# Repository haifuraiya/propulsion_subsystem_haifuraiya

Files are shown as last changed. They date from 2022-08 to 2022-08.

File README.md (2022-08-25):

# propulsion_subsystem_haifuraiya
# Introduction

This Open Research Institute Phase4SPace project repo will be used to develop the proposed Haifuraiya (Japanese:  ハイフライヤー English: High-Flyer) propulsion subsystem for a future HEO mission SmallSat. The repo was created on 8/28/2022.

# Summary

In July/August 2022 the ORI community discussed formalizing a concept for a High Energy Orbit (HEO) 'flyer' satellite, that would have its own propulsion system. The background for the Haifuraiya name and the overall initial concept derivation/top-level goals was discussed at length and is recorded[^1] and its predecessor concept by Jan King W3GEY is directly available[^2]. 

# Team

1. Samudra Haque N3RDX
2. Dan Schultz N8FGV
3. Thomas Denz, KC3ELI

# Special Notes

By special arrangement with its inventor/develpoer, ORI is making available in this repository a public copy of the entire flight hardware designs/firmware build knowledge-base including a comprehensive technical, scientific and industrial documentation set of [The George Washington University][100] [Micro-propulsion and Nanotechnology Laboratory][99]'s successful 2014-2015 BRICSAT-P (US Naval Academy/George Washington University) and 2014-2018 Canyval-X (Yonsei University/NASA GSFC/George Washington University) CubeSat quad-channel electric rocket system as provided in 2015 to NASA, on the condition that it is only used for study/research/experimentation/academic and scientific missions, and no commercial development is allowed. Parts of the technology have been patented (US Patent 10006445) and is available for licensing from The George Washington University. 

The knowledge-base is available [here][101]

If you choose to view/utilize the references (Approximately *3.14GB, 3525 files*), you are advised the knowledge-base contains copyrighted code, and information that was and still could be of a propietary nature thus may have more restrictive licenses than the license under which ORI has organized this repository. Your are restricted from disseminating this repository without the exact same restrictions you are being asked to follow. *While ORI has assurances the information will be able to be replicated (to build ground/engineering/flight hardware) with current production COTS parts -  there is no technical support provided, and all questions are to be redirected to the inventor/developer directly. Contact ORI for further details.* 

# References

[^1]: [Haifuraiya slide presentations (August 2022)][1]
[^2]: [HEO-F Mission Overview Space System Design Concept (November 3, 2014)]

[1:] https://github.com/phase4ground/documents/tree/master/Papers_Articles_Presentations/Slide_Presentations/haifuraiya/   
[2:] https://github.com/phase4ground/documents/blob/master/Papers_Articles_Presentations/Slide_Presentations/haifuraiya/HEO-F_Mission%20Overview.pptx  
[99:]https://mpnl.seas.gwu.edu/
[100:] https://www.gwu.edu
[101:] TBD

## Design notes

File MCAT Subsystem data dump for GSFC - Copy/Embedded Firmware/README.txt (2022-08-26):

3/24/2015 Samudra Haque samudra@gwu.edu GWU MAE MpNL
This codebase requires Netburner NANO54415 network development kit (NNDK).
It depends upon the Netburner RTOS and libraries obtained through the typical free developer license, which depends upon the use of an unmodified netburner module, hence the use of a daughter board approach for the Control Unit in a Mini-PCI Express connector/latch.

www.netburner.com

The codebase is 6C. Developed for the BRICSAT-P platform originally (Oct, 2015). Any .s19 extension file is a hex binary to be downloaded to a netburner NANO54415 target. GROUNDTESTING and FLIGHT modes enable/disable verbosity.

Choose the configuration you need to compile for, from the NBECLIPSE project properties page. 

Future versions:
(from e-mail to CANYVAL-X GSFC/GWU team of 3/16/2015) 

3. For the next few steps, leading to the Month of April, with Azimi's help from GSFC I propose to send Yonsei team (or Phil@Yonsei) my planned software mods are as follows:

2A. 3/15/2015 - COMPLETED - Initial load of MCAT canyval will be the 6C flight code of BRICSAT. No Changes. Command Set 6C. No I2C. Serial Comms only.

2B.3/16/2015 - Version 6D - Modification of low-level timing trigger pulse duration to accomodate Canyval IES (Inductive Energy Storage) specs instead of Bricsat IES specs. This will increase slightly increase the on-time of the IGBT in clamped inductive storage operation, No other changes. No I2C. Serial Comms only. Adjustment of command set for firing rates in five segments A...F to represent likely conops. Currently, this is 1/10/20/30/40/50 Hz. Is this sufficient ?

4. The following steps will be done when practical .... between GWU/GSFC collaboration. (Requires use of a backup MCAT Canyval subsystem or the MCAT Bricsat subsystem, and Azimi Benham's GOMSPACE I2C).

2C.  Version 6E - Addition of I2C comms with interface between Serial Command Buffer / I2C RX, and Telemetry Buffer / I2C TX modules. Commands will be programmed and tested from a GOMSPACE (or any other compatible multi-master I2C device at 400 kHz baud rate) to demo  I2C functions. No changes to command set 6C, unless minor and requested by CANYVAL flight team and approved by Phil.

2D. Version 6F - Addition of current sensor functionality, storage of sensor events, transfer of sensor events to I2C telemetry buffer, testing of Polling feature of sensor events via Telemetry buffer on the I2C bus.

Brief Explanation of the low-level timing routines:
This system uses a hardware DMA timer (could be any hardware timer) that is programmable and executes an interrupt-service routine that inspects the value of the time slice counter. Depending upon the hardware timer values, and the programmed counts, different low-level events can be actuated via the GPIO pins of the Control Unit. This behavior is intended to be implemented as several timing sources, allowing variable pulse repetition rate of different thruster channels, and event triggers, but in this implementation is limited to a single source of timing. That said, for a more complex treatment of the options available, refer to US Patent Appl. 14/462,127 and See Note 4 of Schematic MCAT-CANYVAL-BPL-5X1.pdf document.

Actual timing figures are generated using MATLAB DMATIMERV4 script, so ask the technical contact at GWU for proper use.

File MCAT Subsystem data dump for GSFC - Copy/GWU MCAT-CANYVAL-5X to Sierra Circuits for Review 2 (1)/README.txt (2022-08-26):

There are 13 gerber files per PCB set.

The ASSY files are the correct bill of materials

For schematics/board layouts suggestion, see the Eagle directory in the top of the folder tree.

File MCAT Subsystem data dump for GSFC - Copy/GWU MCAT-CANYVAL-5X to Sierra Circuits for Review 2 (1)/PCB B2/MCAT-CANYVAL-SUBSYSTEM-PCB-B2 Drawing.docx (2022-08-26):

Layer Files (V7A prefix)
L1/TopSignal/Component | CMP
L2/TopGround | LY2
L3/Power Plane 1 | L3
L14/Power Plane 2 | L14
L15/BottomGround | L15
L16/BottomSignal/Solder | SOL
Silk Screen CMP | PLC
Silk Screen SOL | PLS
Solder Stop Mask CMP | STC
Solder Stop Mask SOL | STS
Cream Frame CMP | CRC
Cream Frame SOL | CRS
Excellen Drill Data | DDD

X-ray image of PCB displayed on next page.

PCB DRAWING

Subsystem: MCAT | ASSY: MCAT-CANYVAL | P/N: T2 | REV: 5X | 201502241100

By Samudra Haque (samudra@gwu.edu) and George Teel (gteel@gwu.edu), George Washington University, 2/23/2015

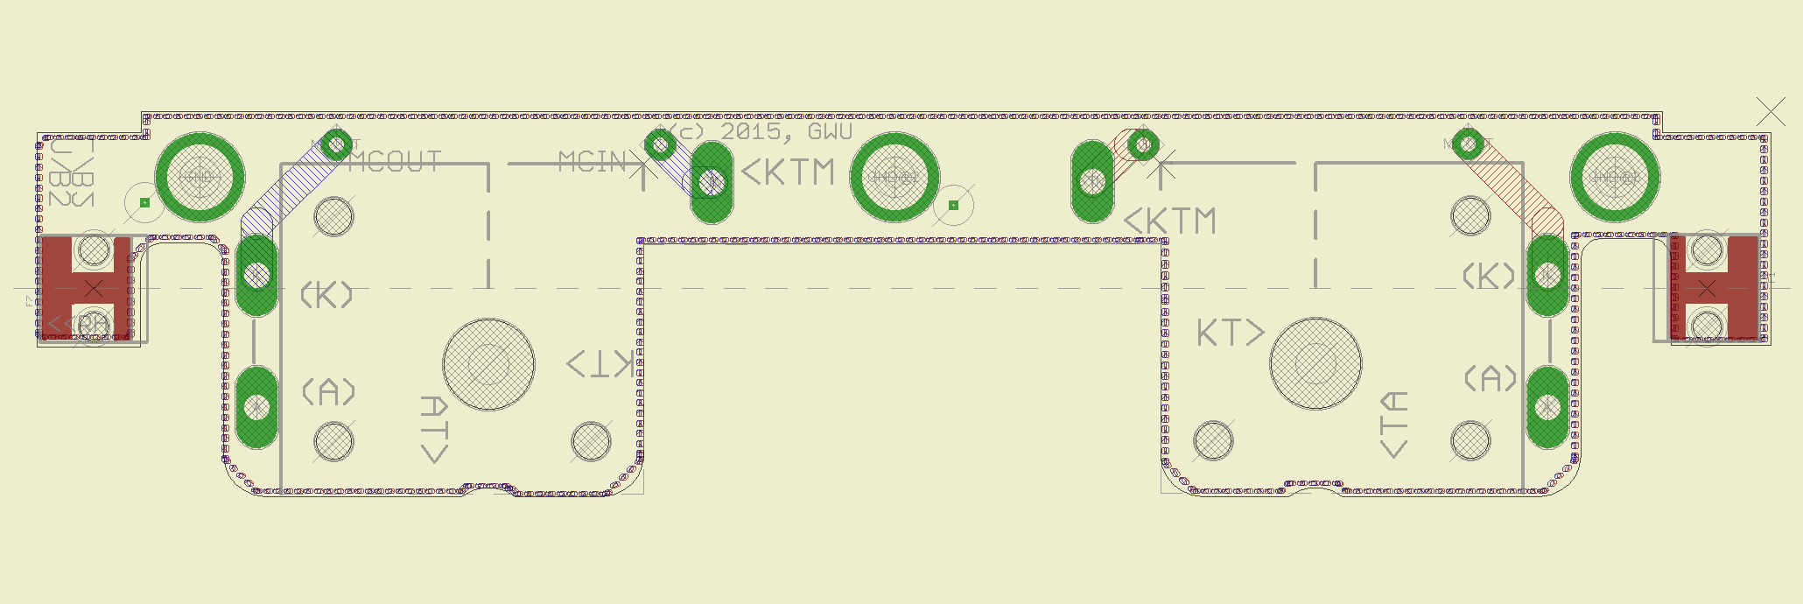
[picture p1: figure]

Notes (unless otherwise specified)

1. Fab per IPC-600G Class 2
2. Material
  a. Lead Free Assembly Compliant, NELCO 7000-3 Toughened POLYIMIDE Laminate & PrEPREG or equiv.
  b. Finished Thickness to be 0.062” +/- .005”
  c. Total of 6 layers with 2 oz. CU ON ALL LAYERS.
  d. FLAMMABILITY RATING: 94 V-O Min.
3. Size: Cut and mill to outline shown; . Datum is BoTTOM/TOP RIGHT CORNER or RIGHT EDGE w/SHARP corner
4. DRILLING: DRILL HOLES PER SCHED. PLATE THROUGH HOLES WITH COPPER, 0.001” THICK MIN.
5. MILLING: PCB OUTLINE PROVIDED
6. ALL HOLE SIZES SPEC. AFTER PLATING.
7. HOLE LOCATION ToL. ARE +/- .003” IN REL. To CTR.
8. FINISH:
  a. HASL
  b. SOLDER MASK OVER BARE COPPER (SMOBC) USING Liquid PHOTO IMAGEABLE (LPI)
  c. COLOR: BOTH SIDES, COLOR BLUE,
  d. SILKSCREEN: WHITE.

Layer functions

L1/Top Signal/Top – 2 Oz Cu.

L2/Top Ground – 2 Oz Cu.

L3/Power Plane 1 – 2 Oz Cu.

L14/Power Plane 2 – 2 Oz Cu.

L15/Bottom Ground – 2 Oz Cu.

L16/Bottom Signal/Bottom – 2 Oz Cu.

MCAT-CANYVAL-B2-5X. 83.82 mm L x 18.64 mm W.

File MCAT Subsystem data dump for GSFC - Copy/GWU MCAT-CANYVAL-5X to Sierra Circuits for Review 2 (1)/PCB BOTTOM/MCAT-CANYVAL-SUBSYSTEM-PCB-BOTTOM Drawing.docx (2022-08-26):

Layer Files
L1/TopSignal/Component | CMP
L2/TopGround | LY2
L3/Power Plane 1 | L3
L14/Power Plane 2 | L14
L15/BottomGround | L15
L16/BottomSignal/Solder | SOL
Silk Screen CMP | PLC
Silk Screen SOL | PLS
Solder Stop Mask CMP | STC
Solder Stop Mask SOL | STS
Cream Frame CMP | CRC
Cream Frame SOL | CRS
Excellen Drill Data | DDD

X-ray image of PCB displayed on next page.

PCB DRAWING

Subsystem: MCAT | ASSY: MCAT-CANYVAL | P/N: BOTTOM | REV: 5X | 201502241100

By Samudra Haque (samudra@gwu.edu) and George Teel (gteel@gwu.edu), George Washington University, 2/23/2015

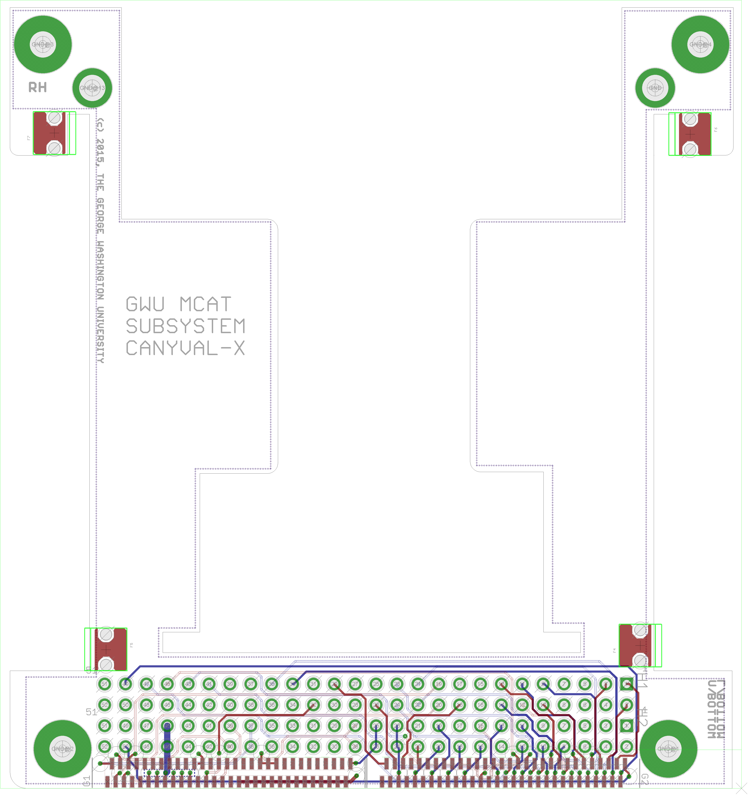
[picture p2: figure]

Notes (unless otherwise specified)

1. Fab per IPC-600G Class 2
2. Material
  a. Lead Free Assembly Compliant, ARLON 85NT or equiv.
  b. Finished Thickness to be 0.062” +/- .005”
  c. Total of 6 layers with 2 oz. CU ON ALL LAYERS.
3. Size: Cut and mill to outline shown; . Datum is BoTTOM RIGHT CORNER
4. DRILLING: DRILL HOLES PER SCHED. PLATE THROUGH HOLES WITH COPPER, 0.001” THICK MIN.
5. MILLING: PCB OUTLINE PROVIDED
6. ALL HOLE SIZES SPEC. AFTER PLATING.
7. HOLE LOCATION ToL. ARE +/- .003” IN REL. To CTR.
8. FINISH:
  a. HASL
  b. SOLDER MASK OVER BARE COPPER (SMOBC) USING Liquid PHOTO IMAGEABLE (LPI)
  c. COLOR: BOTH SIDES, COLOR BLUE,
  d. SILKSCREEN: WHITE.
9. GERBER LAYERS MAY BE NAMED DIFFERENT, BUT LAYERS 1,2,3,14,15,16 (top>BOTTOM)
10. BOTTOM EDGE HAS CONNECTORS UPTO BOARD EDGE or VERY CLOSE, CRITICAL POSITION.
11. BOARD DIM APPROX.

Layer functions

L1/Top Signal/Top – 2 Oz Cu.

L2/Top Ground – 2 Oz Cu.

L3/Power Plane 1 – 2 Oz Cu.

L14/Power Plane 2 – 2 Oz Cu.

L15/Bottom Ground – 2 Oz Cu.

L16/Bottom Signal/Bottom – 2 Oz Cu.

MCAT-CANYVAL-BOTTOM-5X. ~~ 95 mm L x 88 mm W.

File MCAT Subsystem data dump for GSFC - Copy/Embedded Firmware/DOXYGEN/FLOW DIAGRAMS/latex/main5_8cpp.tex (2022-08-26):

\hypertarget{main5_8cpp}{}\section{C\+:/\+Users/samudra/\+Google Drive/\+M\+C\+A\+T4\+C\+U\+F\+S\+W/main5.cpp File Reference}
\label{main5_8cpp}\index{C\+:/\+Users/samudra/\+Google Drive/\+M\+C\+A\+T4\+C\+U\+F\+S\+W/main5.\+cpp@{C\+:/\+Users/samudra/\+Google Drive/\+M\+C\+A\+T4\+C\+U\+F\+S\+W/main5.\+cpp}}
{\ttfamily \#include \char`\"{}predef.\+h\char`\"{}}\\*
{\ttfamily \#include $<$stdio.\+h$>$}\\*
{\ttfamily \#include $<$ctype.\+h$>$}\\*
{\ttfamily \#include $<$startnet.\+h$>$}\\*
{\ttfamily \#include $<$autoupdate.\+h$>$}\\*
{\ttfamily \#include $<$dhcpclient.\+h$>$}\\*
{\ttfamily \#include $<$taskmon.\+h$>$}\\*
{\ttfamily \#include $<$smarttrap.\+h$>$}\\*
{\ttfamily \#include $<$string.\+h$>$}\\*
{\ttfamily \#include $<$math.\+h$>$}\\*
{\ttfamily \#include $<$assert.\+h$>$}\\*
{\ttfamily \#include $<$multichanneli2c.\+h$>$}\\*
{\ttfamily \#include $<$sim5441x.\+h$>$}\\*
{\ttfamily \#include $<$cfinter.\+h$>$}\\*
{\ttfamily \#include $<$iostream$>$}\\*
{\ttfamily \#include $<$iomanip$>$}\\*
{\ttfamily \#include $<$string$>$}\\*
{\ttfamily \#include \char`\"{}mcat\+\_\+config.\+h\char`\"{}}\\*
{\ttfamily \#include \char`\"{}mcat\+\_\+cmd\+\_\+packet.\+h\char`\"{}}\\*
{\ttfamily \#include \char`\"{}mcat\+\_\+timing.\+h\char`\"{}}\\*
Include dependency graph for main5.\+cpp\+:
\nopagebreak
\begin{figure}[H]
\begin{center}
\leavevmode

\end{center}
\end{figure}
\subsection*{Functions}
\begin{DoxyCompactItemize}
\item 
void \hyperlink{main5_8cpp_af3350bd69feae78ebcd4f766916eeb67}{parse\+C\+M\+D\+Packet} (char C\+M\+D\+Packet\mbox{[}I2\+C\+\_\+\+M\+A\+X\+\_\+\+B\+U\+F\+\_\+\+S\+I\+Z\+E\mbox{]})
\item 
void \hyperlink{main5_8cpp_aa3032893ba2f121a12d4cecf88277580}{parse\+Block\+G} (string Block\+G)
\item 
void \hyperlink{main5_8cpp_ab8ff54f4b027d2dfb6d3b63194fc15a4}{parse\+Block\+C\+U} (string Block\+C\+U)
\item 
void \hyperlink{main5_8cpp_a72e39dd7a2538b8b278f927ffd051bde}{parse\+Block\+I\+P\+D} (string Block\+I\+P\+D)
\item 
void \hyperlink{main5_8cpp_a8109658a433363943c469e7743c238ab}{parse\+Block\+P\+P\+U} (string Block\+P\+P\+U)
\item 
B\+Y\+T\+E \hyperlink{main5_8cpp_a22bb15ed96d4891d904b55838e451124}{Ascii2\+Byte} (char $\ast$buf)
\item 
void \hyperlink{main5_8cpp_ad16e5e62f3579a7048e6b981b172885e}{menu} (void)
\item 
void \hyperlink{main5_8cpp_ace7b2f4c33cbf41f3a43c7be01ff7aec}{User\+Main} (void $\ast$pd)
\item 
void \hyperlink{main5_8cpp_a486c7b37eb37847afaeeb6c73de398b9}{display\+Config} ()
\item 
void \hyperlink{main5_8cpp_a855e0d71fbad695926236f90ac687f35}{do\+Pulses} (void $\ast$pdata)
\item 
void \hyperlink{main5_8cpp_a11ee600b69b27b0bb2d1b5b6e8ece140}{stop\+Pulses} (void $\ast$pdata)
\item 
void \hyperlink{main5_8cpp_a10570e6420ce0f0a076e1e9d3518d305}{init\+D\+M\+A\+T\+I\+M\+E\+R1} ()
\item 
void \hyperlink{main5_8cpp_a7c3f73193878c079945a21075f128059}{Set\+Intc} (long func, int vector, int level, int prio)
\item 
void \hyperlink{main5_8cpp_a8a64466bfb43094b3aec845670b959b4}{set\+Defaults} ()
\item 
void \hyperlink{main5_8cpp_a238885c747f586049b766fa4fcd5ec12}{disable\+All} ()
\item 
void \hyperlink{main5_8cpp_af2e78c1a970cd9490fcc3a5ac8015e6b}{debug\+Print} (string debug\+Msg)
\item 
\hyperlink{main5_8cpp_a89200d64c07024287b4ef31901f44e15}{I\+N\+T\+E\+R\+R\+U\+P\+T} (func\+\_\+isr, 0x2600)
\item 
void \hyperlink{main5_8cpp_acbfa28dfc2a41cc9cea58425f9b75178}{control\+P\+M\+A} (B\+O\+O\+L P\+M\+Flag)
\item 
void \hyperlink{main5_8cpp_ae4e046c7843050c83a5f70092acdbe1d}{control18\+L} (int requested\+Channel, int L\+Flag)
\item 
void \hyperlink{main5_8cpp_ac3f210415061a8b78eaf54a8274ad34a}{control18\+H} (int requested\+Channel, int H\+Flag)
\item 
void \hyperlink{main5_8cpp_a92a0eb6ae19d1612e39cbf1fd318d406}{set\+T\+P1} (long Frequency)
\item 
void \hyperlink{main5_8cpp_a8f5495a6630209795a3fbd7fa61a18e8}{control\+T\+P1} (B\+O\+O\+L T\+P1\+Flag)
\item 
void \hyperlink{main5_8cpp_a0ecec396fb6600a2f4897e7f30318159}{go\+F\+I\+R} ()
\item 
void \hyperlink{main5_8cpp_a2d0df7e0313c78e94bb4fafbc5752d67}{go\+F\+I\+Rfrom\+R\+U\+N} ()
\item 
void \hyperlink{main5_8cpp_ae0014243028b5cd808de963c18d01b11}{go\+F\+I\+Rfrom\+S\+B\+Y} ()
\item 
void \hyperlink{main5_8cpp_affc7dbdeb188c8169ccc6478143538d6}{go\+F\+I\+Rfrom\+I\+D\+L} ()
\item 
void \hyperlink{main5_8cpp_af57dea23daabb0f6e6d27f2ef21c9a54}{go\+R\+U\+N} ()
\item 
void \hyperlink{main5_8cpp_a6d712eb455e679cbf844c6742e7be6a0}{go\+R\+U\+Nfrom\+F\+I\+R} ()
\item 
void \hyperlink{main5_8cpp_a4770c1a01b1be1b23772d600b787d411}{go\+R\+U\+Nfrom\+S\+B\+Y} ()
\item 
void \hyperlink{main5_8cpp_a300391508ed006e4cd4ee0f9f316f3b4}{go\+R\+U\+Nfrom\+I\+D\+L} ()
\item 
void \hyperlink{main5_8cpp_a646dbe8155e1ee44efac5d50a7de878e}{go\+S\+B\+Y} ()
\item 
void \hyperlink{main5_8cpp_ae0ed43b60101aed3be6bea960293275d}{go\+S\+B\+Yfrom\+F\+I\+R} ()
\item 
void \hyperlink{main5_8cpp_a2d0b911e7b667c6a18000005acb28777}{go\+S\+B\+Yfrom\+R\+U\+N} ()
\item 
void \hyperlink{main5_8cpp_a37a57a2b0feb89b22b270931ae440c35}{go\+S\+B\+Yfrom\+I\+D\+L} ()
\item 
void \hyperlink{main5_8cpp_aa8d8f1cf694be5de1ac89b91627c0f51}{go\+I\+D\+L} ()
\item 
void \hyperlink{main5_8cpp_a3e3cc85ab7a91d6808984a0f78a5f9f8}{go\+I\+D\+Lfrom\+S\+B\+Y} ()
\item 
void \hyperlink{main5_8cpp_a690d16feac877ce7000b00e151dffd82}{go\+I\+D\+Lfrom\+R\+U\+N} ()
\item 
void \hyperlink{main5_8cpp_ae5438692f2a6c279129ecc19a91568f2}{go\+I\+D\+Lfrom\+F\+I\+R} ()
\item 
void \hyperlink{main5_8cpp_a9b07c4b395adfe387d12241e7ebaaae6}{set\+New\+Mode} (string cmd\+Mode\+Request, string \hyperlink{main6_c_8cpp_ab996ab5995af95792f5af3586d943d58}{cmd\+Mode\+Current})
\item 
void \hyperlink{main5_8cpp_a5b251dff1da28eda51e8b51bc4b2baf7}{do\+Setup\+I\+O} ()
\end{DoxyCompactItemize}
\subsection*{Variables}
\begin{DoxyCompactItemize}
\item 
string \hyperlink{main5_8cpp_a405cdd34a0ec61abf8c5205c7a8c3182}{cmd\+Version} =\char`\"{}\char`\"{}
\item 
string \hyperlink{main5_8cpp_a8a9767341d04352fccd7068bc1d7c370}{cmd\+Mode} =\char`\"{}\char`\"{}
\item 
string \hyperlink{main5_8cpp_ab996ab5995af95792f5af3586d943d58}{cmd\+Mode\+Current} =\char`\"{}\char`\"{}
\item 
string \hyperlink{main5_8cpp_a56a16ee6139d263a1945acac7412db03}{s\+\_\+cmd\+T\+P1} =\char`\"{}\char`\"{}
\item 
string \hyperlink{main5_8cpp_ac2f7f3d71312267f0daf019326ab81ab}{s\+\_\+cmd\+T\+P2} =\char`\"{}\char`\"{}
\item 
string \hyperlink{main5_8cpp_a684796ab1de60babd3eba75aa8489e68}{s\+\_\+cmd\+T\+P3} =\char`\"{}\char`\"{}
\item 
string \hyperlink{main5_8cpp_a42269eac5fc051ca6c78aae8b6349920}{s\+\_\+cmd\+T\+P4} =\char`\"{}\char`\"{}
\item 
string \hyperlink{main5_8cpp_aa8cec591ab6bc2c30368790b9c90e439}{s\+\_\+cmd\+P\+C\+H1} =\char`\"{}\char`\"{}
\item 
string \hyperlink{main5_8cpp_a0f0135bb7a354979b68358781b0b9a33}{s\+\_\+cmd\+P\+C\+H2} =\char`\"{}\char`\"{}
\item 
string \hyperlink{main5_8cpp_ad027927effdfbc03356897f6784a332f}{s\+\_\+cmd\+P\+C\+H3} =\char`\"{}\char`\"{}
\item 
string \hyperlink{main5_8cpp_a1ee9de883e3c6e7840f6bfd0fdff6976}{s\+\_\+cmd\+P\+C\+H4} =\char`\"{}\char`\"{}
\item 
long \hyperlink{main5_8cpp_ac244c5de67ae1cf2ad9042dd3dd42f5c}{cmd\+T\+P1}
\item 
long \hyperlink{main5_8cpp_a6b5cb6b3c68ceba258ad6741ccf2c2c2}{cmd\+T\+P2}
\item 
long \hyperlink{main5_8cpp_a22ed1f6fb6c9e5132174497269472950}{cmd\+T\+P3}
\item 
long \hyperlink{main5_8cpp_ac556ac861b98bb773707ad78139dd4a7}{cmd\+T\+P4}
\item 
long \hyperlink{main5_8cpp_a6aa9310d261695da6caf50707b289e99}{cmd\+P\+C\+H1}
\item 
long \hyperlink{main5_8cpp_a2ede701ffcc3766012be6e4080433432}{cmd\+P\+C\+H2}
\item 
long \hyperlink{main5_8cpp_a5128aa37f4fea97bace715bd297c7cb4}{cmd\+P\+C\+H3}
\item 
long \hyperlink{main5_8cpp_acda88eaa3c77c003b3a5642a3e28bb48}{cmd\+P\+C\+H4}
\item 
string \hyperlink{main5_8cpp_a37ec136ae86c4b7dc81f393bb1a01af7}{s\+\_\+cmd\+P18\+H1} =\char`\"{}\char`\"{}
\item 
string \hyperlink{main5_8cpp_a46ce373f60085f5900464cd0731fa20e}{s\+\_\+cmd\+P18\+H2} =\char`\"{}\char`\"{}
\item 
string \hyperlink{main5_8cpp_a909acdc96889fb5885793e8bc70b083e}{s\+\_\+cmd\+P18\+H3} =\char`\"{}\char`\"{}
\item 
string \hyperlink{main5_8cpp_a607e82175ad61b864bfa84e686437947}{s\+\_\+cmd\+P18\+H4} =\char`\"{}\char`\"{}
\item 
bool \hyperlink{main5_8cpp_a1a10d6a42e7c3ba1ad7f396b687a7eb7}{cmd\+P18\+H1}
\item 
bool \hyperlink{main5_8cpp_a03df8cc8ee6b4d7ba8a3d2ad50914508}{cmd\+P18\+H2}
\item 
bool \hyperlink{main5_8cpp_aba803fecbea259c5af71f0b9f2e9fa5a}{cmd\+P18\+H3}
\item 
bool \hyperlink{main5_8cpp_a74d16dd0ede9be1a1645027bd2e6fb21}{cmd\+P18\+H4}
\item 
B\+Y\+T\+E \hyperlink{main5_8cpp_a750abfb0120c1735c922980bd47640a5}{buffer} \mbox{[}I2\+C\+\_\+\+M\+A\+X\+\_\+\+B\+U\+F\+\_\+\+S\+I\+Z\+E\mbox{]}
\item 
char \hyperlink{main5_8cpp_af54d77a991da4ba360d594c2589140df}{I2\+C\+Input\+Buffer} \mbox{[}I2\+C\+\_\+\+M\+A\+X\+\_\+\+B\+U\+F\+\_\+\+S\+I\+Z\+E\mbox{]}
\item 
char $\ast$ \hyperlink{main5_8cpp_abed0c40696905e144ed4118061acf700}{inbuf} = \hyperlink{_v2_01main_8cpp_af54d77a991da4ba360d594c2589140df}{I2\+C\+Input\+Buffer}
\item 
B\+Y\+T\+E \hyperlink{main5_8cpp_a92fb5ea5b6a7d108dea33dd07809152d}{address} = \hyperlink{mcatsubsystemconfig_8h_a8fe248bd745b90e2bfe94d8c5fce0a53}{C\+U\+\_\+\+I2\+C\+\_\+\+S\+L\+A\+V\+E\+\_\+\+A\+D\+D\+R}
\item 
B\+Y\+T\+E \hyperlink{main5_8cpp_a6c3dedd37414833dd07e72ee4a642d13}{I2\+C\+Stat}
\end{DoxyCompactItemize}

\subsection{Function Documentation}
\hypertarget{main5_8cpp_a22bb15ed96d4891d904b55838e451124}{}\index{main5.\+cpp@{main5.\+cpp}!Ascii2\+Byte@{Ascii2\+Byte}}
\index{Ascii2\+Byte@{Ascii2\+Byte}!main5.\+cpp@{main5.\+cpp}}
\subsubsection[{Ascii2\+Byte}]{\setlength{\rightskip}{0pt plus 5cm}B\+Y\+T\+E Ascii2\+Byte (
\begin{DoxyParamCaption}
\item[{char $\ast$}]{buf}
\end{DoxyParamCaption}
)}\label{main5_8cpp_a22bb15ed96d4891d904b55838e451124}

Definition at line 914 of file main5.\+cpp.

\hypertarget{main5_8cpp_ac3f210415061a8b78eaf54a8274ad34a}{}\index{main5.\+cpp@{main5.\+cpp}!control18\+H@{control18\+H}}
\index{control18\+H@{control18\+H}!main5.\+cpp@{main5.\+cpp}}
\subsubsection[{control18\+H}]{\setlength{\rightskip}{0pt plus 5cm}void control18\+H (
\begin{DoxyParamCaption}
\item[{int}]{requested\+Channel, }
\item[{int}]{H\+Flag}
\end{DoxyParamCaption}
)}\label{main5_8cpp_ac3f210415061a8b78eaf54a8274ad34a}

Definition at line 331 of file main5.\+cpp.

\hypertarget{main5_8cpp_ae4e046c7843050c83a5f70092acdbe1d}{}\index{main5.\+cpp@{main5.\+cpp}!control18\+L@{control18\+L}}
\index{control18\+L@{control18\+L}!main5.\+cpp@{main5.\+cpp}}
\subsubsection[{control18\+L}]{\setlength{\rightskip}{0pt plus 5cm}void control18\+L (
\begin{DoxyParamCaption}
\item[{int}]{requested\+Channel, }
\item[{int}]{L\+Flag}
\end{DoxyParamCaption}
)}\label{main5_8cpp_ae4e046c7843050c83a5f70092acdbe1d}

Definition at line 268 of file main5.\+cpp.

\hypertarget{main5_8cpp_acbfa28dfc2a41cc9cea58425f9b75178}{}\index{main5.\+cpp@{main5.\+cpp}!control\+P\+M\+A@{control\+P\+M\+A}}
\index{control\+P\+M\+A@{control\+P\+M\+A}!main5.\+cpp@{main5.\+cpp}}
\subsubsection[{control\+P\+M\+A}]{\setlength{\rightskip}{0pt plus 5cm}void control\+P\+M\+A (
\begin{DoxyParamCaption}
\item[{B\+O\+O\+L}]{P\+M\+Flag}
\end{DoxyParamCaption}
)}\label{main5_8cpp_acbfa28dfc2a41cc9cea58425f9b75178}

Definition at line 252 of file main5.\+cpp.

\hypertarget{main5_8cpp_a8f5495a6630209795a3fbd7fa61a18e8}{}\index{main5.\+cpp@{main5.\+cpp}!control\+T\+P1@{control\+T\+P1}}
\index{control\+T\+P1@{control\+T\+P1}!main5.\+cpp@{main5.\+cpp}}
\subsubsection[{control\+T\+P1}]{\setlength{\rightskip}{0pt plus 5cm}void control\+T\+P1 (
\begin{DoxyParamCaption}
\item[{B\+O\+O\+L}]{T\+P1\+Flag}
\end{DoxyParamCaption}
)}\label{main5_8cpp_a8f5495a6630209795a3fbd7fa61a18e8}
from 5270 code set /// D\+O N\+O\+T U\+S\+E Set\+Intc((long) \&func\+\_\+isr, 19, 1, 1); 

Definition at line 420 of file main5.\+cpp.

\hypertarget{main5_8cpp_af2e78c1a970cd9490fcc3a5ac8015e6b}{}\index{main5.\+cpp@{main5.\+cpp}!debug\+Print@{debug\+Print}}
\index{debug\+Print@{debug\+Print}!main5.\+cpp@{main5.\+cpp}}
\subsubsection[{debug\+Print}]{\setlength{\rightskip}{0pt plus 5cm}void debug\+Print (
\begin{DoxyParamCaption}
\item[{string}]{debug\+Msg}
\end{DoxyParamCaption}
)}\label{main5_8cpp_af2e78c1a970cd9490fcc3a5ac8015e6b}

Definition at line 177 of file main5.\+cpp.

\hypertarget{main5_8cpp_a238885c747f586049b766fa4fcd5ec12}{}\index{main5.\+cpp@{main5.\+cpp}!disable\+All@{disable\+All}}
\index{disable\+All@{disable\+All}!main5.\+cpp@{main5.\+cpp}}
\subsubsection[{disable\+All}]{\setlength{\rightskip}{0pt plus 5cm}void disable\+All (
\begin{DoxyParamCaption}
{}
\end{DoxyParamCaption}
)}\label{main5_8cpp_a238885c747f586049b766fa4fcd5ec12}

Definition at line 609 of file main5.\+cpp.

\hypertarget{main5_8cpp_a486c7b37eb37847afaeeb6c73de398b9}{}\index{main5.\+cpp@{main5.\+cpp}!display\+Config@{display\+Config}}
\index{display\+Config@{display\+Config}!main5.\+cpp@{main5.\+cpp}}
\subsubsection[{display\+Config}]{\setlength{\rightskip}{0pt plus 5cm}void display\+Config (
\begin{DoxyParamCaption}
{}
\end{DoxyParamCaption}
)}\label{main5_8cpp_a486c7b37eb37847afaeeb6c73de398b9}
\hypertarget{main5_8cpp_a855e0d71fbad695926236f90ac687f35}{}\index{main5.\+cpp@{main5.\+cpp}!do\+Pulses@{do\+Pulses}}
\index{do\+Pulses@{do\+Pulses}!main5.\+cpp@{main5.\+cpp}}
\subsubsection[{do\+Pulses}]{\setlength{\rightskip}{0pt plus 5cm}void do\+Pulses (
\begin{DoxyParamCaption}
\item[{void $\ast$}]{pdata}
\end{DoxyParamCaption}
)}\label{main5_8cpp_a855e0d71fbad695926236f90ac687f35}

Definition at line 627 of file main5.\+cpp.

\hypertarget{main5_8cpp_a5b251dff1da28eda51e8b51bc4b2baf7}{}\index{main5.\+cpp@{main5.\+cpp}!do\+Setup\+I\+O@{do\+Setup\+I\+O}}
\index{do\+Setup\+I\+O@{do\+Setup\+I\+O}!main5.\+cpp@{main5.\+cpp}}
\subsubsection[{do\+Setup\+I\+O}]{\setlength{\rightskip}{0pt plus 5cm}void do\+Setup\+I\+O (
\begin{DoxyParamCaption}
{}
\end{DoxyParamCaption}
)}\label{main5_8cpp_a5b251dff1da28eda51e8b51bc4b2baf7}

Definition at line 670 of file main5.\+cpp.

\hypertarget{main5_8cpp_a0ecec396fb6600a2f4897e7f30318159}{}\index{main5.\+cpp@{main5.\+cpp}!go\+F\+I\+R@{go\+F\+I\+R}}
\index{go\+F\+I\+R@{go\+F\+I\+R}!main5.\+cpp@{main5.\+cpp}}
\subsubsection[{go\+F\+I\+R}]{\setlength{\rightskip}{0pt plus 5cm}void go\+F\+I\+R (
\begin{DoxyParamCaption}
{}
\end{DoxyParamCaption}
)}\label{main5_8cpp_a0ecec396fb6600a2f4897e7f30318159}

Definition at line 454 of file main5.\+cpp.

\hypertarget{main5_8cpp_affc7dbdeb188c8169ccc6478143538d6}{}\index{main5.\+cpp@{main5.\+cpp}!go\+F\+I\+Rfrom\+I\+D\+L@{go\+F\+I\+Rfrom\+I\+D\+L}}
\index{go\+F\+I\+Rfrom\+I\+D\+L@{go\+F\+I\+Rfrom\+I\+D\+L}!main5.\+cpp@{main5.\+cpp}}
\subsubsection[{go\+F\+I\+Rfrom\+I\+D\+L}]{\setlength{\rightskip}{0pt plus 5cm}void go\+F\+I\+Rfrom\+I\+D\+L (
\begin{DoxyParamCaption}
{}
\end{DoxyParamCaption}
)}\label{main5_8cpp_affc7dbdeb188c8169ccc6478143538d6}

Definition at line 467 of file main5.\+cpp.

\hypertarget{main5_8cpp_a2d0df7e0313c78e94bb4fafbc5752d67}{}\index{main5.\+cpp@{main5.\+cpp}!go\+F\+I\+Rfrom\+R\+U\+N@{go\+F\+I\+Rfrom\+R\+U\+N}}
\index{go\+F\+I\+Rfrom\+R\+U\+N@{go\+F\+I\+Rfrom\+R\+U\+N}!main5.\+cpp@{main5.\+cpp}}
\subsubsection[{go\+F\+I\+Rfrom\+R\+U\+N}]{\setlength{\rightskip}{0pt plus 5cm}void go\+F\+I\+Rfrom\+R\+U\+N (
\begin{DoxyParamCaption}
{}
\end{DoxyParamCaption}
)}\label{main5_8cpp_a2d0df7e0313c78e94bb4fafbc5752d67}

Definition at line 459 of file main5.\+cpp.

\hypertarget{main5_8cpp_ae0014243028b5cd808de963c18d01b11}{}\index{main5.\+cpp@{main5.\+cpp}!go\+F\+I\+Rfrom\+S\+B\+Y@{go\+F\+I\+Rfrom\+S\+B\+Y}}
\index{go\+F\+I\+Rfrom\+S\+B\+Y@{go\+F\+I\+Rfrom\+S\+B\+Y}!main5.\+cpp@{main5.\+cpp}}
\subsubsection[{go\+F\+I\+Rfrom\+S\+B\+Y}]{\setlength{\rightskip}{0pt plus 5cm}void go\+F\+I\+Rfrom\+S\+B\+Y (
\begin{DoxyParamCaption}
{}
\end{DoxyParamCaption}
)}\label{main5_8cpp_ae0014243028b5cd808de963c18d01b11}

Definition at line 463 of file main5.\+cpp.

\hypertarget{main5_8cpp_aa8d8f1cf694be5de1ac89b91627c0f51}{}\index{main5.\+cpp@{main5.\+cpp}!go\+I\+D\+L@{go\+I\+D\+L}}
\index{go\+I\+D\+L@{go\+I\+D\+L}!main5.\+cpp@{main5.\+cpp}}
\subsubsection[{go\+I\+D\+L}]{\setlength{\rightskip}{0pt plus 5cm}void go\+I\+D\+L (
\begin{DoxyParamCaption}
{}
\end{DoxyParamCaption}
)}\label{main5_8cpp_aa8d8f1cf694be5de1ac89b91627c0f51}

Definition at line 512 of file main5.\+cpp.

\hypertarget{main5_8cpp_ae5438692f2a6c279129ecc19a91568f2}{}\index{main5.\+cpp@{main5.\+cpp}!go\+I\+D\+Lfrom\+F\+I\+R@{go\+I\+D\+Lfrom\+F\+I\+R}}
\index{go\+I\+D\+Lfrom\+F\+I\+R@{go\+I\+D\+Lfrom\+F\+I\+R}!main5.\+cpp@{main5.\+cpp}}
\subsubsection[{go\+I\+D\+Lfrom\+F\+I\+R}]{\setlength{\rightskip}{0pt plus 5cm}void go\+I\+D\+Lfrom\+F\+I\+R (
\begin{DoxyParamCaption}
{}
\end{DoxyParamCaption}
)}\label{main5_8cpp_ae5438692f2a6c279129ecc19a91568f2}

Definition at line 525 of file main5.\+cpp.

\hypertarget{main5_8cpp_a690d16feac877ce7000b00e151dffd82}{}\index{main5.\+cpp@{main5.\+cpp}!go\+I\+D\+Lfrom\+R\+U\+N@{go\+I\+D\+Lfrom\+R\+U\+N}}
\index{go\+I\+D\+Lfrom\+R\+U\+N@{go\+I\+D\+Lfrom\+R\+U\+N}!main5.\+cpp@{main5.\+cpp}}
\subsubsection[{go\+I\+D\+Lfrom\+R\+U\+N}]{\setlength{\rightskip}{0pt plus 5cm}void go\+I\+D\+Lfrom\+R\+U\+N (
\begin{DoxyParamCaption}
{}
\end{DoxyParamCaption}
)}\label{main5_8cpp_a690d16feac877ce7000b00e151dffd82}

Definition at line 521 of file main5.\+cpp.

\hypertarget{main5_8cpp_a3e3cc85ab7a91d6808984a0f78a5f9f8}{}\index{main5.\+cpp@{main5.\+cpp}!go\+I\+D\+Lfrom\+S\+B\+Y@{go\+I\+D\+Lfrom\+S\+B\+Y}}
\index{go\+I\+D\+Lfrom\+S\+B\+Y@{go\+I\+D\+Lfrom\+S\+B\+Y}!main5.\+cpp@{main5.\+cpp}}
\subsubsection[{go\+I\+D\+Lfrom\+S\+B\+Y}]{\setlength{\rightskip}{0pt plus 5cm}void go\+I\+D\+Lfrom\+S\+B\+Y (
\begin{DoxyParamCaption}
{}
\end{DoxyParamCaption}
)}\label{main5_8cpp_a3e3cc85ab7a91d6808984a0f78a5f9f8}

Definition at line 517 of file main5.\+cpp.

\hypertarget{main5_8cpp_af57dea23daabb0f6e6d27f2ef21c9a54}{}\index{main5.\+cpp@{main5.\+cpp}!go\+R\+U\+N@{go\+R\+U\+N}}
\index{go\+R\+U\+N@{go\+R\+U\+N}!main5.\+cpp@{main5.\+cpp}}
\subsubsection[{go\+R\+U\+N}]{\setlength{\rightskip}{0pt plus 5cm}void go\+R\+U\+N (
\begin{DoxyParamCaption}
{}
\end{DoxyParamCaption}
)}\label{main5_8cpp_af57dea23daabb0f6e6d27f2ef21c9a54}

Definition at line 472 of file main5.\+cpp.

\hypertarget{main5_8cpp_a6d712eb455e679cbf844c6742e7be6a0}{}\index{main5.\+cpp@{main5.\+cpp}!go\+R\+U\+Nfrom\+F\+I\+R@{go\+R\+U\+Nfrom\+F\+I\+R}}
\index{go\+R\+U\+Nfrom\+F\+I\+R@{go\+R\+U\+Nfrom\+F\+I\+R}!main5.\+cpp@{main5.\+cpp}}
\subsubsection[{go\+R\+U\+Nfrom\+F\+I\+R}]{\setlength{\rightskip}{0pt plus 5cm}void go\+R\+U\+Nfrom\+F\+I\+R (
\begin{DoxyParamCaption}
{}
\end{DoxyParamCaption}
)}\label{main5_8cpp_a6d712eb455e679cbf844c6742e7be6a0}

Definition at line 481 of file main5.\+cpp.

\hypertarget{main5_8cpp_a300391508ed006e4cd4ee0f9f316f3b4}{}\index{main5.\+cpp@{main5.\+cpp}!go\+R\+U\+Nfrom\+I\+D\+L@{go\+R\+U\+Nfrom\+I\+D\+L}}
\index{go\+R\+U\+Nfrom\+I\+D\+L@{go\+R\+U\+Nfrom\+I\+D\+L}!main5.\+cpp@{main5.\+cpp}}
\subsubsection[{go\+R\+U\+Nfrom\+I\+D\+L}]{\setlength{\rightskip}{0pt plus 5cm}void go\+R\+U\+Nfrom\+I\+D\+L (
\begin{DoxyParamCaption}
{}
\end{DoxyParamCaption}
)}\label{main5_8cpp_a300391508ed006e4cd4ee0f9f316f3b4}

Definition at line 489 of file main5.\+cpp.

\hypertarget{main5_8cpp_a4770c1a01b1be1b23772d600b787d411}{}\index{main5.\+cpp@{main5.\+cpp}!go\+R\+U\+Nfrom\+S\+B\+Y@{go\+R\+U\+Nfrom\+S\+B\+Y}}
\index{go\+R\+U\+Nfrom\+S\+B\+Y@{go\+R\+U\+Nfrom\+S\+B\+Y}!main5.\+cpp@{main5.\+cpp}}
\subsubsection[{go\+R\+U\+Nfrom\+S\+B\+Y}]{\setlength{\rightskip}{0pt plus 5cm}void go\+R\+U\+Nfrom\+S\+B\+Y (
\begin{DoxyParamCaption}
{}
\end{DoxyParamCaption}
)}\label{main5_8cpp_a4770c1a01b1be1b23772d600b787d411}

Definition at line 485 of file main5.\+cpp.

\hypertarget{main5_8cpp_a646dbe8155e1ee44efac5d50a7de878e}{}\index{main5.\+cpp@{main5.\+cpp}!go\+S\+B\+Y@{go\+S\+B\+Y}}
\index{go\+S\+B\+Y@{go\+S\+B\+Y}!main5.\+cpp@{main5.\+cpp}}
\subsubsection[{go\+S\+B\+Y}]{\setlength{\rightskip}{0pt plus 5cm}void go\+S\+B\+Y (
\begin{DoxyParamCaption}
{}
\end{DoxyParamCaption}
)}\label{main5_8cpp_a646dbe8155e1ee44efac5d50a7de878e}

Definition at line 494 of file main5.\+cpp.

\hypertarget{main5_8cpp_ae0ed43b60101aed3be6bea960293275d}{}\index{main5.\+cpp@{main5.\+cpp}!go\+S\+B\+Yfrom\+F\+I\+R@{go\+S\+B\+Yfrom\+F\+I\+R}}
\index{go\+S\+B\+Yfrom\+F\+I\+R@{go\+S\+B\+Yfrom\+F\+I\+R}!main5.\+cpp@{main5.\+cpp}}
\subsubsection[{go\+S\+B\+Yfrom\+F\+I\+R}]{\setlength{\rightskip}{0pt plus 5cm}void go\+S\+B\+Yfrom\+F\+I\+R (
\begin{DoxyParamCaption}
{}
\end{DoxyParamCaption}
)}\label{main5_8cpp_ae0ed43b60101aed3be6bea960293275d}

Definition at line 499 of file main5.\+cpp.

\hypertarget{main5_8cpp_a37a57a2b0feb89b22b270931ae440c35}{}\index{main5.\+cpp@{main5.\+cpp}!go\+S\+B\+Yfrom\+I\+D\+L@{go\+S\+B\+Yfrom\+I\+D\+L}}
\index{go\+S\+B\+Yfrom\+I\+D\+L@{go\+S\+B\+Yfrom\+I\+D\+L}!main5.\+cpp@{main5.\+cpp}}
\subsubsection[{go\+S\+B\+Yfrom\+I\+D\+L}]{\setlength{\rightskip}{0pt plus 5cm}void go\+S\+B\+Yfrom\+I\+D\+L (
\begin{DoxyParamCaption}
{}
\end{DoxyParamCaption}
)}\label{main5_8cpp_a37a57a2b0feb89b22b270931ae440c35}

Definition at line 507 of file main5.\+cpp.

\hypertarget{main5_8cpp_a2d0b911e7b667c6a18000005acb28777}{}\index{main5.\+cpp@{main5.\+cpp}!go\+S\+B\+Yfrom\+R\+U\+N@{go\+S\+B\+Yfrom\+R\+U\+N}}
\index{go\+S\+B\+Yfrom\+R\+U\+N@{go\+S\+B\+Yfrom\+R\+U\+N}!main5.\+cpp@{main5.\+cpp}}
\subsubsection[{go\+S\+B\+Yfrom\+R\+U\+N}]{\setlength{\rightskip}{0pt plus 5cm}void go\+S\+B\+Yfrom\+R\+U\+N (
\begin{DoxyParamCaption}
{}
\end{DoxyParamCaption}
)}\label{main5_8cpp_a2d0b911e7b667c6a18000005acb28777}

Definition at line 503 of file main5.\+cpp.

\hypertarget{main5_8cpp_a10570e6420ce0f0a076e1e9d3518d305}{}\index{main5.\+cpp@{main5.\+cpp}!init\+D\+M\+A\+T\+I\+M\+E\+R1@{init\+D\+M\+A\+T\+I\+M\+E\+R1}}
\index{init\+D\+M\+A\+T\+I\+M\+E\+R1@{init\+D\+M\+A\+T\+I\+M\+E\+R1}!main5.\+cpp@{main5.\+cpp}}
\subsubsection[{init\+D\+M\+A\+T\+I\+M\+E\+R1}]{\setlength{\rightskip}{0pt plus 5cm}void init\+D\+M\+A\+T\+I\+M\+E\+R1 (
\begin{DoxyParamCaption}
{}
\end{DoxyParamCaption}
)}\label{main5_8cpp_a10570e6420ce0f0a076e1e9d3518d305}
from 5270 code set /// D\+O N\+O\+T U\+S\+E Set\+Intc((long) \&func\+\_\+isr, 19, 1, 1); 

Definition at line 655 of file main5.\+cpp.

\hypertarget{main5_8cpp_a89200d64c07024287b4ef31901f44e15}{}\index{main5.\+cpp@{main5.\+cpp}!I\+N\+T\+E\+R\+R\+U\+P\+T@{I\+N\+T\+E\+R\+R\+U\+P\+T}}
\index{I\+N\+T\+E\+R\+R\+U\+P\+T@{I\+N\+T\+E\+R\+R\+U\+P\+T}!main5.\+cpp@{main5.\+cpp}}
\subsubsection[{I\+N\+T\+E\+R\+R\+U\+P\+T}]{\setlength{\rightskip}{0pt plus 5cm}I\+N\+T\+E\+R\+R\+U\+P\+T (
\begin{DoxyParamCaption}
\item[{func\+\_\+isr}]{, }
\item[{0x2600}]{}
\end{DoxyParamCaption}
)}\label{main5_8cpp_a89200d64c07024287b4ef31901f44e15}

Definition at line 185 of file main5.\+cpp.

\hypertarget{main5_8cpp_ad16e5e62f3579a7048e6b981b172885e}{}\index{main5.\+cpp@{main5.\+cpp}!menu@{menu}}
\index{menu@{menu}!main5.\+cpp@{main5.\+cpp}}
\subsubsection[{menu}]{\setlength{\rightskip}{0pt plus 5cm}void menu (
\begin{DoxyParamCaption}
\item[{void}]{}
\end{DoxyParamCaption}
)}\label{main5_8cpp_ad16e5e62f3579a7048e6b981b172885e}

Definition at line 932 of file main5.\+cpp.

\hypertarget{main5_8cpp_ab8ff54f4b027d2dfb6d3b63194fc15a4}{}\index{main5.\+cpp@{main5.\+cpp}!parse\+Block\+C\+U@{parse\+Block\+C\+U}}
\index{parse\+Block\+C\+U@{parse\+Block\+C\+U}!main5.\+cpp@{main5.\+cpp}}
\subsubsection[{parse\+Block\+C\+U}]{\setlength{\rightskip}{0pt plus 5cm}void parse\+Block\+C\+U (
\begin{DoxyParamCaption}
\item[{string}]{Block\+C\+U}
\end{DoxyParamCaption}
)}\label{main5_8cpp_ab8ff54f4b027d2dfb6d3b63194fc15a4}

Definition at line 792 of file main5.\+cpp.

\hypertarget{main5_8cpp_aa3032893ba2f121a12d4cecf88277580}{}\index{main5.\+cpp@{main5.\+cpp}!parse\+Block\+G@{parse\+Block\+G}}
\index{parse\+Block\+G@{parse\+Block\+G}!main5.\+cpp@{main5.\+cpp}}
\subsubsection[{parse\+Block\+G}]{\setlength{\rightskip}{0pt plus 5cm}void parse\+Block\+G (
\begin{DoxyParamCaption}
\item[{string}]{Block\+G}
\end{DoxyParamCaption}
)}\label{main5_8cpp_aa3032893ba2f121a12d4cecf88277580}

Definition at line 782 of file main5.\+cpp.

\hypertarget{main5_8cpp_a72e39dd7a2538b8b278f927ffd051bde}{}\index{main5.\+cpp@{main5.\+cpp}!parse\+Block\+I\+P\+D@{parse\+Block\+I\+P\+D}}
\index{parse\+Block\+I\+P\+D@{parse\+Block\+I\+P\+D}!main5.\+cpp@{main5.\+cpp}}
\subsubsection[{parse\+Block\+I\+P\+D}]{\setlength{\rightskip}{0pt plus 5cm}void parse\+Block\+I\+P\+D (
\begin{DoxyParamCaption}
\item[{string}]{Block\+I\+P\+D}
\end{DoxyParamCaption}
)}\label{main5_8cpp_a72e39dd7a2538b8b278f927ffd051bde}

Definition at line 802 of file main5.\+cpp.

\hypertarget{main5_8cpp_a8109658a433363943c469e7743c238ab}{}\index{main5.\+cpp@{main5.\+cpp}!parse\+Block\+P\+P\+U@{parse\+Block\+P\+P\+U}}
\index{parse\+Block\+P\+P\+U@{parse\+Block\+P\+P\+U}!main5.\+cpp@{main5.\+cpp}}
\subsubsection[{parse\+Block\+P\+P\+U}]{\setlength{\rightskip}{0pt plus 5cm}void parse\+Block\+P\+P\+U (
\begin{DoxyParamCaption}
\item[{string}]{Block\+P\+P\+U}
\end{DoxyParamCaption}
)}\label{main5_8cpp_a8109658a433363943c469e7743c238ab}

Definition at line 857 of file main5.\+cpp.

\hypertarget{main5_8cpp_af3350bd69feae78ebcd4f766916eeb67}{}\index{main5.\+cpp@{main5.\+cpp}!parse\+C\+M\+D\+Packet@{parse\+C\+M\+D\+Packet}}
\index{parse\+C\+M\+D\+Packet@{parse\+C\+M\+D\+Packet}!main5.\+cpp@{main5.\+cpp}}
\subsubsection[{parse\+C\+M\+D\+Packet}]{\setlength{\rightskip}{0pt plus 5cm}void parse\+C\+M\+D\+Packet (
\begin{DoxyParamCaption}
\item[{char}]{C\+M\+D\+Packet\mbox{[}\+I2\+C\+\_\+\+M\+A\+X\+\_\+\+B\+U\+F\+\_\+\+S\+I\+Z\+E\mbox{]}}
\end{DoxyParamCaption}
)}\label{main5_8cpp_af3350bd69feae78ebcd4f766916eeb67}

Definition at line 721 of file main5.\+cpp.

\hypertarget{main5_8cpp_a8a64466bfb43094b3aec845670b959b4}{}\index{main5.\+cpp@{main5.\+cpp}!set\+Defaults@{set\+Defaults}}
\index{set\+Defaults@{set\+Defaults}!main5.\+cpp@{main5.\+cpp}}
\subsubsection[{set\+Defaults}]{\setlength{\rightskip}{0pt plus 5cm}void set\+Defaults (
\begin{DoxyParamCaption}
{}
\end{DoxyParamCaption}
)}\label{main5_8cpp_a8a64466bfb43094b3aec845670b959b4}

Definition at line 616 of file main5.\+cpp.

\hypertarget{main5_8cpp_a7c3f73193878c079945a21075f128059}{}\index{main5.\+cpp@{main5.\+cpp}!Set\+Intc@{Set\+Intc}}
\index{Set\+Intc@{Set\+Intc}!main5.\+cpp@{main5.\+cpp}}
\subsubsection[{Set\+Intc}]{\setlength{\rightskip}{0pt plus 5cm}void Set\+Intc (
\begin{DoxyParamCaption}
\item[{long}]{func, }
\item[{int}]{vector, }
\item[{int}]{level, }
\item[{int}]{prio}
\end{DoxyParamCaption}
)}\label{main5_8cpp_a7c3f73193878c079945a21075f128059}
\hypertarget{main5_8cpp_a9b07c4b395adfe387d12241e7ebaaae6}{}\index{main5.\+cpp@{main5.\+cpp}!set\+New\+Mode@{set\+New\+Mode}}
\index{set\+New\+Mode@{set\+New\+Mode}!main5.\+cpp@{main5.\+cpp}}
\subsubsection[{set\+New\+Mode}]{\setlength{\rightskip}{0pt plus 5cm}void set\+New\+Mode (
\begin{DoxyParamCaption}
\item[{string}]{cmd\+Mode\+Request, }
\item[{string}]{cmd\+Mode\+Current}
\end{DoxyParamCaption}
)}\label{main5_8cpp_a9b07c4b395adfe387d12241e7ebaaae6}

Definition at line 532 of file main5.\+cpp.

\hypertarget{main5_8cpp_a92a0eb6ae19d1612e39cbf1fd318d406}{}\index{main5.\+cpp@{main5.\+cpp}!set\+T\+P1@{set\+T\+P1}}
\index{set\+T\+P1@{set\+T\+P1}!main5.\+cpp@{main5.\+cpp}}
\subsubsection[{set\+T\+P1}]{\setlength{\rightskip}{0pt plus 5cm}void set\+T\+P1 (
\begin{DoxyParamCaption}
\item[{long}]{Frequency}
\end{DoxyParamCaption}
)}\label{main5_8cpp_a92a0eb6ae19d1612e39cbf1fd318d406}

Definition at line 399 of file main5.\+cpp.

\hypertarget{main5_8cpp_a11ee600b69b27b0bb2d1b5b6e8ece140}{}\index{main5.\+cpp@{main5.\+cpp}!stop\+Pulses@{stop\+Pulses}}
\index{stop\+Pulses@{stop\+Pulses}!main5.\+cpp@{main5.\+cpp}}
\subsubsection[{stop\+Pulses}]{\setlength{\rightskip}{0pt plus 5cm}void stop\+Pulses (
\begin{DoxyParamCaption}
\item[{void $\ast$}]{pdata}
\end{DoxyParamCaption}
)}\label{main5_8cpp_a11ee600b69b27b0bb2d1b5b6e8ece140}
\hypertarget{main5_8cpp_ace7b2f4c33cbf41f3a43c7be01ff7aec}{}\index{main5.\+cpp@{main5.\+cpp}!User\+Main@{User\+Main}}
\index{User\+Main@{User\+Main}!main5.\+cpp@{main5.\+cpp}}
\subsubsection[{User\+Main}]{\setlength{\rightskip}{0pt plus 5cm}void User\+Main (
\begin{DoxyParamCaption}
\item[{void $\ast$}]{pd}
\end{DoxyParamCaption}
)}\label{main5_8cpp_ace7b2f4c33cbf41f3a43c7be01ff7aec}
Thruster Channel P18 activation section

C\+H1-\/4

End Thruster Channel P18 activation section 

Definition at line 957 of file main5.\+cpp.

\subsection{Variable Documentation}
\hypertarget{main5_8cpp_a92fb5ea5b6a7d108dea33dd07809152d}{}\index{main5.\+cpp@{main5.\+cpp}!address@{address}}
\index{address@{address}!main5.\+cpp@{main5.\+cpp}}
\subsubsection[{address}]{\setlength{\rightskip}{0pt plus 5cm}B\+Y\+T\+E address = {\bf C\+U\+\_\+\+I2\+C\+\_\+\+S\+L\+A\+V\+E\+\_\+\+A\+D\+D\+R}}\label{main5_8cpp_a92fb5ea5b6a7d108dea33dd07809152d}

Definition at line 174 of file main5.\+cpp.

\hypertarget{main5_8cpp_a750abfb0120c1735c922980bd47640a5}{}\index{main5.\+cpp@{main5.\+cpp}!buffer@{buffer}}
\index{buffer@{buffer}!main5.\+cpp@{main5.\+cpp}}
\subsubsection[{buffer}]{\setlength{\rightskip}{0pt plus 5cm}B\+Y\+T\+E buffer\mbox{[}I2\+C\+\_\+\+M\+A\+X\+\_\+\+B\+U\+F\+\_\+\+S\+I\+Z\+E\mbox{]}}\label{main5_8cpp_a750abfb0120c1735c922980bd47640a5}

Definition at line 171 of file main5.\+cpp.

\hypertarget{main5_8cpp_a8a9767341d04352fccd7068bc1d7c370}{}\index{main5.\+cpp@{main5.\+cpp}!cmd\+Mode@{cmd\+Mode}}
\index{cmd\+Mode@{cmd\+Mode}!main5.\+cpp@{main5.\+cpp}}
\subsubsection[{cmd\+Mode}]{\setlength{\rightskip}{0pt plus 5cm}string cmd\+Mode =\char`\"{}\char`\"{}}\label{main5_8cpp_a8a9767341d04352fccd7068bc1d7c370}

Definition at line 101 of file main5.\+cpp.

\hypertarget{main5_8cpp_ab996ab5995af95792f5af3586d943d58}{}\index{main5.\+cpp@{main5.\+cpp}!cmd\+Mode\+Current@{cmd\+Mode\+Current}}
\index{cmd\+Mode\+Current@{cmd\+Mode\+Current}!main5.\+cpp@{main5.\+cpp}}
\subsubsection[{cmd\+Mode\+Current}]{\setlength{\rightskip}{0pt plus 5cm}string cmd\+Mode\+Current =\char`\"{}\char`\"{}}\label{main5_8cpp_ab996ab5995af95792f5af3586d943d58}

Definition at line 102 of file main5.\+cpp.

\hypertarget{main5_8cpp_a1a10d6a42e7c3ba1ad7f396b687a7eb7}{}\index{main5.\+cpp@{main5.\+cpp}!cmd\+P18\+H1@{cmd\+P18\+H1}}
\index{cmd\+P18\+H1@{cmd\+P18\+H1}!main5.\+cpp@{main5.\+cpp}}
\subsubsection[{cmd\+P18\+H1}]{\setlength{\rightskip}{0pt plus 5cm}bool cmd\+P18\+H1}\label{main5_8cpp_a1a10d6a42e7c3ba1ad7f396b687a7eb7}

Definition at line 116 of file main5.\+cpp.

\hypertarget{main5_8cpp_a03df8cc8ee6b4d7ba8a3d2ad50914508}{}\index{main5.\+cpp@{main5.\+cpp}!cmd\+P18\+H2@{cmd\+P18\+H2}}
\index{cmd\+P18\+H2@{cmd\+P18\+H2}!main5.\+cpp@{main5.\+cpp}}
\subsubsection[{cmd\+P18\+H2}]{\setlength{\rightskip}{0pt plus 5cm}bool cmd\+P18\+H2}\label{main5_8cpp_a03df8cc8ee6b4d7ba8a3d2ad50914508}

Definition at line 116 of file main5.\+cpp.

\hypertarget{main5_8cpp_aba803fecbea259c5af71f0b9f2e9fa5a}{}\index{main5.\+cpp@{main5.\+cpp}!cmd\+P18\+H3@{cmd\+P18\+H3}}
\index{cmd\+P18\+H3@{cmd\+P18\+H3}!main5.\+cpp@{main5.\+cpp}}
\subsubsection[{cmd\+P18\+H3}]{\setlength{\rightskip}{0pt plus 5cm}bool cmd\+P18\+H3}\label{main5_8cpp_aba803fecbea259c5af71f0b9f2e9fa5a}

Definition at line 116 of file main5.\+cpp.

\hypertarget{main5_8cpp_a74d16dd0ede9be1a1645027bd2e6fb21}{}\index{main5.\+cpp@{main5.\+cpp}!cmd\+P18\+H4@{cmd\+P18\+H4}}
\index{cmd\+P18\+H4@{cmd\+P18\+H4}!main5.\+cpp@{main5.\+cpp}}
\subsubsection[{cmd\+P18\+H4}]{\setlength{\rightskip}{0pt plus 5cm}bool cmd\+P18\+H4}\label{main5_8cpp_a74d16dd0ede9be1a1645027bd2e6fb21}

Definition at line 116 of file main5.\+cpp.

\hypertarget{main5_8cpp_a6aa9310d261695da6caf50707b289e99}{}\index{main5.\+cpp@{main5.\+cpp}!cmd\+P\+C\+H1@{cmd\+P\+C\+H1}}
\index{cmd\+P\+C\+H1@{cmd\+P\+C\+H1}!main5.\+cpp@{main5.\+cpp}}
\subsubsection[{cmd\+P\+C\+H1}]{\setlength{\rightskip}{0pt plus 5cm}long cmd\+P\+C\+H1}\label{main5_8cpp_a6aa9310d261695da6caf50707b289e99}

Definition at line 111 of file main5.\+cpp.

\hypertarget{main5_8cpp_a2ede701ffcc3766012be6e4080433432}{}\index{main5.\+cpp@{main5.\+cpp}!cmd\+P\+C\+H2@{cmd\+P\+C\+H2}}
\index{cmd\+P\+C\+H2@{cmd\+P\+C\+H2}!main5.\+cpp@{main5.\+cpp}}
\subsubsection[{cmd\+P\+C\+H2}]{\setlength{\rightskip}{0pt plus 5cm}long cmd\+P\+C\+H2}\label{main5_8cpp_a2ede701ffcc3766012be6e4080433432}

Definition at line 111 of file main5.\+cpp.

\hypertarget{main5_8cpp_a5128aa37f4fea97bace715bd297c7cb4}{}\index{main5.\+cpp@{main5.\+cpp}!cmd\+P\+C\+H3@{cmd\+P\+C\+H3}}
\index{cmd\+P\+C\+H3@{cmd\+P\+C\+H3}!main5.\+cpp@{main5.\+cpp}}
\subsubsection[{cmd\+P\+C\+H3}]{\setlength{\rightskip}{0pt plus 5cm}long cmd\+P\+C\+H3}\label{main5_8cpp_a5128aa37f4fea97bace715bd297c7cb4}

Definition at line 111 of file main5.\+cpp.

\hypertarget{main5_8cpp_acda88eaa3c77c003b3a5642a3e28bb48}{}\index{main5.\+cpp@{main5.\+cpp}!cmd\+P\+C\+H4@{cmd\+P\+C\+H4}}
\index{cmd\+P\+C\+H4@{cmd\+P\+C\+H4}!main5.\+cpp@{main5.\+cpp}}
\subsubsection[{cmd\+P\+C\+H4}]{\setlength{\rightskip}{0pt plus 5cm}long cmd\+P\+C\+H4}\label{main5_8cpp_acda88eaa3c77c003b3a5642a3e28bb48}

Definition at line 111 of file main5.\+cpp.

\hypertarget{main5_8cpp_ac244c5de67ae1cf2ad9042dd3dd42f5c}{}\index{main5.\+cpp@{main5.\+cpp}!cmd\+T\+P1@{cmd\+T\+P1}}
\index{cmd\+T\+P1@{cmd\+T\+P1}!main5.\+cpp@{main5.\+cpp}}
\subsubsection[{cmd\+T\+P1}]{\setlength{\rightskip}{0pt plus 5cm}long cmd\+T\+P1}\label{main5_8cpp_ac244c5de67ae1cf2ad9042dd3dd42f5c}

Definition at line 111 of file main5.\+cpp.

\hypertarget{main5_8cpp_a6b5cb6b3c68ceba258ad6741ccf2c2c2}{}\index{main5.\+cpp@{main5.\+cpp}!cmd\+T\+P2@{cmd\+T\+P2}}
\index{cmd\+T\+P2@{cmd\+T\+P2}!main5.\+cpp@{main5.\+cpp}}
\subsubsection[{cmd\+T\+P2}]{\setlength{\rightskip}{0pt plus 5cm}long cmd\+T\+P2}\label{main5_8cpp_a6b5cb6b3c68ceba258ad6741ccf2c2c2}

Definition at line 111 of file main5.\+cpp.

\hypertarget{main5_8cpp_a22ed1f6fb6c9e5132174497269472950}{}\index{main5.\+cpp@{main5.\+cpp}!cmd\+T\+P3@{cmd\+T\+P3}}
\index{cmd\+T\+P3@{cmd\+T\+P3}!main5.\+cpp@{main5.\+cpp}}
\subsubsection[{cmd\+T\+P3}]{\setlength{\rightskip}{0pt plus 5cm}long cmd\+T\+P3}\label{main5_8cpp_a22ed1f6fb6c9e5132174497269472950}

Definition at line 111 of file main5.\+cpp.

\hypertarget{main5_8cpp_ac556ac861b98bb773707ad78139dd4a7}{}\index{main5.\+cpp@{main5.\+cpp}!cmd\+T\+P4@{cmd\+T\+P4}}
\index{cmd\+T\+P4@{cmd\+T\+P4}!main5.\+cpp@{main5.\+cpp}}
\subsubsection[{cmd\+T\+P4}]{\setlength{\rightskip}{0pt plus 5cm}long cmd\+T\+P4}\label{main5_8cpp_ac556ac861b98bb773707ad78139dd4a7}

Definition at line 111 of file main5.\+cpp.

\hypertarget{main5_8cpp_a405cdd34a0ec61abf8c5205c7a8c3182}{}\index{main5.\+cpp@{main5.\+cpp}!cmd\+Version@{cmd\+Version}}
\index{cmd\+Version@{cmd\+Version}!main5.\+cpp@{main5.\+cpp}}
\subsubsection[{cmd\+Version}]{\setlength{\rightskip}{0pt plus 5cm}string cmd\+Version =\char`\"{}\char`\"{}}\label{main5_8cpp_a405cdd34a0ec61abf8c5205c7a8c3182}

Definition at line 100 of file main5.\+cpp.

\hypertarget{main5_8cpp_af54d77a991da4ba360d594c2589140df}{}\index{main5.\+cpp@{main5.\+cpp}!I2\+C\+Input\+Buffer@{I2\+C\+Input\+Buffer}}
\index{I2\+C\+Input\+Buffer@{I2\+C\+Input\+Buffer}!main5.\+cpp@{main5.\+cpp}}
\subsubsection[{I2\+C\+Input\+Buffer}]{\setlength{\rightskip}{0pt plus 5cm}char I2\+C\+Input\+Buffer\mbox{[}I2\+C\+\_\+\+M\+A\+X\+\_\+\+B\+U\+F\+\_\+\+S\+I\+Z\+E\mbox{]}}\label{main5_8cpp_af54d77a991da4ba360d594c2589140df}

Definition at line 172 of file main5.\+cpp.

\hypertarget{main5_8cpp_a6c3dedd37414833dd07e72ee4a642d13}{}\index{main5.\+cpp@{main5.\+cpp}!I2\+C\+Stat@{I2\+C\+Stat}}
\index{I2\+C\+Stat@{I2\+C\+Stat}!main5.\+cpp@{main5.\+cpp}}
\subsubsection[{I2\+C\+Stat}]{\setlength{\rightskip}{0pt plus 5cm}B\+Y\+T\+E I2\+C\+Stat}\label{main5_8cpp_a6c3dedd37414833dd07e72ee4a642d13}

Definition at line 175 of file main5.\+cpp.

\hypertarget{main5_8cpp_abed0c40696905e144ed4118061acf700}{}\index{main5.\+cpp@{main5.\+cpp}!inbuf@{inbuf}}
\index{inbuf@{inbuf}!main5.\+cpp@{main5.\+cpp}}
\subsubsection[{inbuf}]{\setlength{\rightskip}{0pt plus 5cm}char$\ast$ inbuf = {\bf I2\+C\+Input\+Buffer}}\label{main5_8cpp_abed0c40696905e144ed4118061acf700}

Definition at line 173 of file main5.\+cpp.

\hypertarget{main5_8cpp_a37ec136ae86c4b7dc81f393bb1a01af7}{}\index{main5.\+cpp@{main5.\+cpp}!s\+\_\+cmd\+P18\+H1@{s\+\_\+cmd\+P18\+H1}}
\index{s\+\_\+cmd\+P18\+H1@{s\+\_\+cmd\+P18\+H1}!main5.\+cpp@{main5.\+cpp}}
\subsubsection[{s\+\_\+cmd\+P18\+H1}]{\setlength{\rightskip}{0pt plus 5cm}string s\+\_\+cmd\+P18\+H1 =\char`\"{}\char`\"{}}\label{main5_8cpp_a37ec136ae86c4b7dc81f393bb1a01af7}

Definition at line 112 of file main5.\+cpp.

\hypertarget{main5_8cpp_a46ce373f60085f5900464cd0731fa20e}{}\index{main5.\+cpp@{main5.\+cpp}!s\+\_\+cmd\+P18\+H2@{s\+\_\+cmd\+P18\+H2}}
\index{s\+\_\+cmd\+P18\+H2@{s\+\_\+cmd\+P18\+H2}!main5.\+cpp@{main5.\+cpp}}
\subsubsection[{s\+\_\+cmd\+P18\+H2}]{\setlength{\rightskip}{0pt plus 5cm}string s\+\_\+cmd\+P18\+H2 =\char`\"{}\char`\"{}}\label{main5_8cpp_a46ce373f60085f5900464cd0731fa20e}

Definition at line 113 of file main5.\+cpp.

\hypertarget{main5_8cpp_a909acdc96889fb5885793e8bc70b083e}{}\index{main5.\+cpp@{main5.\+cpp}!s\+\_\+cmd\+P18\+H3@{s\+\_\+cmd\+P18\+H3}}
\index{s\+\_\+cmd\+P18\+H3@{s\+\_\+cmd\+P18\+H3}!main5.\+cpp@{main5.\+cpp}}
\subsubsection[{s\+\_\+cmd\+P18\+H3}]{\setlength{\rightskip}{0pt plus 5cm}string s\+\_\+cmd\+P18\+H3 =\char`\"{}\char`\"{}}\label{main5_8cpp_a909acdc96889fb5885793e8bc70b083e}

Definition at line 114 of file main5.\+cpp.

\hypertarget{main5_8cpp_a607e82175ad61b864bfa84e686437947}{}\index{main5.\+cpp@{main5.\+cpp}!s\+\_\+cmd\+P18\+H4@{s\+\_\+cmd\+P18\+H4}}
\index{s\+\_\+cmd\+P18\+H4@{s\+\_\+cmd\+P18\+H4}!main5.\+cpp@{main5.\+cpp}}
\subsubsection[{s\+\_\+cmd\+P18\+H4}]{\setlength{\rightskip}{0pt plus 5cm}string s\+\_\+cmd\+P18\+H4 =\char`\"{}\char`\"{}}\label{main5_8cpp_a607e82175ad61b864bfa84e686437947}

Definition at line 115 of file main5.\+cpp.

\hypertarget{main5_8cpp_aa8cec591ab6bc2c30368790b9c90e439}{}\index{main5.\+cpp@{main5.\+cpp}!s\+\_\+cmd\+P\+C\+H1@{s\+\_\+cmd\+P\+C\+H1}}
\index{s\+\_\+cmd\+P\+C\+H1@{s\+\_\+cmd\+P\+C\+H1}!main5.\+cpp@{main5.\+cpp}}
\subsubsection[{s\+\_\+cmd\+P\+C\+H1}]{\setlength{\rightskip}{0pt plus 5cm}string s\+\_\+cmd\+P\+C\+H1 =\char`\"{}\char`\"{}}\label{main5_8cpp_aa8cec591ab6bc2c30368790b9c90e439}

Definition at line 107 of file main5.\+cpp.

\hypertarget{main5_8cpp_a0f0135bb7a354979b68358781b0b9a33}{}\index{main5.\+cpp@{main5.\+cpp}!s\+\_\+cmd\+P\+C\+H2@{s\+\_\+cmd\+P\+C\+H2}}
\index{s\+\_\+cmd\+P\+C\+H2@{s\+\_\+cmd\+P\+C\+H2}!main5.\+cpp@{main5.\+cpp}}
\subsubsection[{s\+\_\+cmd\+P\+C\+H2}]{\setlength{\rightskip}{0pt plus 5cm}string s\+\_\+cmd\+P\+C\+H2 =\char`\"{}\char`\"{}}\label{main5_8cpp_a0f0135bb7a354979b68358781b0b9a33}

Definition at line 108 of file main5.\+cpp.

\hypertarget{main5_8cpp_ad027927effdfbc03356897f6784a332f}{}\index{main5.\+cpp@{main5.\+cpp}!s\+\_\+cmd\+P\+C\+H3@{s\+\_\+cmd\+P\+C\+H3}}
\index{s\+\_\+cmd\+P\+C\+H3@{s\+\_\+cmd\+P\+C\+H3}!main5.\+cpp@{main5.\+cpp}}
\subsubsection[{s\+\_\+cmd\+P\+C\+H3}]{\setlength{\rightskip}{0pt plus 5cm}string s\+\_\+cmd\+P\+C\+H3 =\char`\"{}\char`\"{}}\label{main5_8cpp_ad027927effdfbc03356897f6784a332f}

Definition at line 109 of file main5.\+cpp.

\hypertarget{main5_8cpp_a1ee9de883e3c6e7840f6bfd0fdff6976}{}\index{main5.\+cpp@{main5.\+cpp}!s\+\_\+cmd\+P\+C\+H4@{s\+\_\+cmd\+P\+C\+H4}}
\index{s\+\_\+cmd\+P\+C\+H4@{s\+\_\+cmd\+P\+C\+H4}!main5.\+cpp@{main5.\+cpp}}
\subsubsection[{s\+\_\+cmd\+P\+C\+H4}]{\setlength{\rightskip}{0pt plus 5cm}string s\+\_\+cmd\+P\+C\+H4 =\char`\"{}\char`\"{}}\label{main5_8cpp_a1ee9de883e3c6e7840f6bfd0fdff6976}

Definition at line 110 of file main5.\+cpp.

\hypertarget{main5_8cpp_a56a16ee6139d263a1945acac7412db03}{}\index{main5.\+cpp@{main5.\+cpp}!s\+\_\+cmd\+T\+P1@{s\+\_\+cmd\+T\+P1}}
\index{s\+\_\+cmd\+T\+P1@{s\+\_\+cmd\+T\+P1}!main5.\+cpp@{main5.\+cpp}}
\subsubsection[{s\+\_\+cmd\+T\+P1}]{\setlength{\rightskip}{0pt plus 5cm}string s\+\_\+cmd\+T\+P1 =\char`\"{}\char`\"{}}\label{main5_8cpp_a56a16ee6139d263a1945acac7412db03}

Definition at line 103 of file main5.\+cpp.

\hypertarget{main5_8cpp_ac2f7f3d71312267f0daf019326ab81ab}{}\index{main5.\+cpp@{main5.\+cpp}!s\+\_\+cmd\+T\+P2@{s\+\_\+cmd\+T\+P2}}
\index{s\+\_\+cmd\+T\+P2@{s\+\_\+cmd\+T\+P2}!main5.\+cpp@{main5.\+cpp}}
\subsubsection[{s\+\_\+cmd\+T\+P2}]{\setlength{\rightskip}{0pt plus 5cm}string s\+\_\+cmd\+T\+P2 =\char`\"{}\char`\"{}}\label{main5_8cpp_ac2f7f3d71312267f0daf019326ab81ab}

Definition at line 104 of file main5.\+cpp.

\hypertarget{main5_8cpp_a684796ab1de60babd3eba75aa8489e68}{}\index{main5.\+cpp@{main5.\+cpp}!s\+\_\+cmd\+T\+P3@{s\+\_\+cmd\+T\+P3}}
\index{s\+\_\+cmd\+T\+P3@{s\+\_\+cmd\+T\+P3}!main5.\+cpp@{main5.\+cpp}}
\subsubsection[{s\+\_\+cmd\+T\+P3}]{\setlength{\rightskip}{0pt plus 5cm}string s\+\_\+cmd\+T\+P3 =\char`\"{}\char`\"{}}\label{main5_8cpp_a684796ab1de60babd3eba75aa8489e68}

Definition at line 105 of file main5.\+cpp.

\hypertarget{main5_8cpp_a42269eac5fc051ca6c78aae8b6349920}{}\index{main5.\+cpp@{main5.\+cpp}!s\+\_\+cmd\+T\+P4@{s\+\_\+cmd\+T\+P4}}
\index{s\+\_\+cmd\+T\+P4@{s\+\_\+cmd\+T\+P4}!main5.\+cpp@{main5.\+cpp}}
\subsubsection[{s\+\_\+cmd\+T\+P4}]{\setlength{\rightskip}{0pt plus 5cm}string s\+\_\+cmd\+T\+P4 =\char`\"{}\char`\"{}}\label{main5_8cpp_a42269eac5fc051ca6c78aae8b6349920}

Definition at line 106 of file main5.\+cpp.

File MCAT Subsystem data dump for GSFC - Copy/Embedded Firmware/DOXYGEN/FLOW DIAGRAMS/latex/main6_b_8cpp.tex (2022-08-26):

\hypertarget{main6_b_8cpp}{}\section{C\+:/\+Users/samudra/\+Google Drive/\+M\+C\+A\+T4\+C\+U\+F\+S\+W/main6\+B.cpp File Reference}
\label{main6_b_8cpp}\index{C\+:/\+Users/samudra/\+Google Drive/\+M\+C\+A\+T4\+C\+U\+F\+S\+W/main6\+B.\+cpp@{C\+:/\+Users/samudra/\+Google Drive/\+M\+C\+A\+T4\+C\+U\+F\+S\+W/main6\+B.\+cpp}}
{\ttfamily \#include \char`\"{}predef.\+h\char`\"{}}\\*
{\ttfamily \#include $<$stdio.\+h$>$}\\*
{\ttfamily \#include $<$ctype.\+h$>$}\\*
{\ttfamily \#include $<$startnet.\+h$>$}\\*
{\ttfamily \#include $<$autoupdate.\+h$>$}\\*
{\ttfamily \#include $<$dhcpclient.\+h$>$}\\*
{\ttfamily \#include $<$taskmon.\+h$>$}\\*
{\ttfamily \#include $<$smarttrap.\+h$>$}\\*
{\ttfamily \#include $<$string.\+h$>$}\\*
{\ttfamily \#include $<$math.\+h$>$}\\*
{\ttfamily \#include $<$assert.\+h$>$}\\*
{\ttfamily \#include $<$multichanneli2c.\+h$>$}\\*
{\ttfamily \#include $<$sim5441x.\+h$>$}\\*
{\ttfamily \#include $<$cfinter.\+h$>$}\\*
{\ttfamily \#include $<$iostream$>$}\\*
{\ttfamily \#include $<$iomanip$>$}\\*
{\ttfamily \#include $<$string$>$}\\*
{\ttfamily \#include \char`\"{}mcat\+\_\+config.\+h\char`\"{}}\\*
{\ttfamily \#include \char`\"{}mcat\+\_\+cmd\+\_\+packet.\+h\char`\"{}}\\*
{\ttfamily \#include \char`\"{}mcat\+\_\+timing.\+h\char`\"{}}\\*
{\ttfamily \#include \char`\"{}periph\+\_\+clocks.\+h\char`\"{}}\\*
Include dependency graph for main6\+B.\+cpp\+:
\nopagebreak
\begin{figure}[H]
\begin{center}
\leavevmode
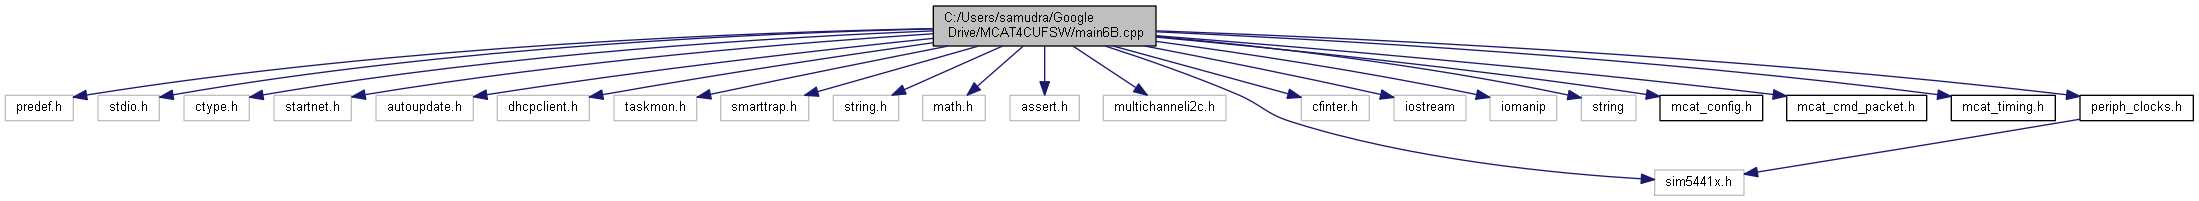
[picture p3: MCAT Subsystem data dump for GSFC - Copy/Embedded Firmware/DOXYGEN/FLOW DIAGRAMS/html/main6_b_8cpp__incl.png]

\end{center}
\end{figure}
\subsection*{Functions}
\begin{DoxyCompactItemize}
\item 
void \hyperlink{main6_b_8cpp_af3350bd69feae78ebcd4f766916eeb67}{parse\+C\+M\+D\+Packet} (char C\+M\+D\+Packet\mbox{[}I2\+C\+\_\+\+M\+A\+X\+\_\+\+B\+U\+F\+\_\+\+S\+I\+Z\+E\mbox{]})
\item 
void \hyperlink{main6_b_8cpp_aa3032893ba2f121a12d4cecf88277580}{parse\+Block\+G} (string Block\+G)
\item 
void \hyperlink{main6_b_8cpp_ab8ff54f4b027d2dfb6d3b63194fc15a4}{parse\+Block\+C\+U} (string Block\+C\+U)
\item 
void \hyperlink{main6_b_8cpp_a72e39dd7a2538b8b278f927ffd051bde}{parse\+Block\+I\+P\+D} (string Block\+I\+P\+D)
\item 
void \hyperlink{main6_b_8cpp_a8109658a433363943c469e7743c238ab}{parse\+Block\+P\+P\+U} (string Block\+P\+P\+U)
\item 
B\+Y\+T\+E \hyperlink{main6_b_8cpp_a22bb15ed96d4891d904b55838e451124}{Ascii2\+Byte} (char $\ast$buf)
\item 
void \hyperlink{main6_b_8cpp_ad16e5e62f3579a7048e6b981b172885e}{menu} (void)
\item 
void \hyperlink{main6_b_8cpp_ace7b2f4c33cbf41f3a43c7be01ff7aec}{User\+Main} (void $\ast$pd)
\item 
void \hyperlink{main6_b_8cpp_a486c7b37eb37847afaeeb6c73de398b9}{display\+Config} ()
\item 
void \hyperlink{main6_b_8cpp_a11ee600b69b27b0bb2d1b5b6e8ece140}{stop\+Pulses} (void $\ast$pdata)
\item 
void \hyperlink{main6_b_8cpp_a10570e6420ce0f0a076e1e9d3518d305}{init\+D\+M\+A\+T\+I\+M\+E\+R1} ()
\item 
void \hyperlink{main6_b_8cpp_a7c3f73193878c079945a21075f128059}{Set\+Intc} (long func, int vector, int level, int prio)
\item 
void \hyperlink{main6_b_8cpp_a8a64466bfb43094b3aec845670b959b4}{set\+Defaults} ()
\item 
void \hyperlink{main6_b_8cpp_a238885c747f586049b766fa4fcd5ec12}{disable\+All} ()
\item 
void \hyperlink{main6_b_8cpp_af2e78c1a970cd9490fcc3a5ac8015e6b}{debug\+Print} (string debug\+Msg)
\item 
\hyperlink{main6_b_8cpp_a89200d64c07024287b4ef31901f44e15}{I\+N\+T\+E\+R\+R\+U\+P\+T} (func\+\_\+isr, 0x2600)
\item 
void \hyperlink{main6_b_8cpp_acbfa28dfc2a41cc9cea58425f9b75178}{control\+P\+M\+A} (B\+O\+O\+L P\+M\+Flag)
\item 
void \hyperlink{main6_b_8cpp_ae4e046c7843050c83a5f70092acdbe1d}{control18\+L} (int requested\+Channel, int L\+Flag)
\item 
void \hyperlink{main6_b_8cpp_a2f5a551d47d5257bf34046aede82024e}{control18\+Hmanual} (int requested\+Channel, int H\+Flag)
\item 
void \hyperlink{main6_b_8cpp_a92a0eb6ae19d1612e39cbf1fd318d406}{set\+T\+P1} (long Frequency)
\item 
void \hyperlink{main6_b_8cpp_a8f5495a6630209795a3fbd7fa61a18e8}{control\+T\+P1} (B\+O\+O\+L T\+P1\+Flag)
\item 
void \hyperlink{main6_b_8cpp_a0ecec396fb6600a2f4897e7f30318159}{go\+F\+I\+R} ()
\item 
void \hyperlink{main6_b_8cpp_a2d0df7e0313c78e94bb4fafbc5752d67}{go\+F\+I\+Rfrom\+R\+U\+N} ()
\item 
void \hyperlink{main6_b_8cpp_ae0014243028b5cd808de963c18d01b11}{go\+F\+I\+Rfrom\+S\+B\+Y} ()
\item 
void \hyperlink{main6_b_8cpp_affc7dbdeb188c8169ccc6478143538d6}{go\+F\+I\+Rfrom\+I\+D\+L} ()
\item 
void \hyperlink{main6_b_8cpp_af57dea23daabb0f6e6d27f2ef21c9a54}{go\+R\+U\+N} ()
\item 
void \hyperlink{main6_b_8cpp_a6d712eb455e679cbf844c6742e7be6a0}{go\+R\+U\+Nfrom\+F\+I\+R} ()
\item 
void \hyperlink{main6_b_8cpp_a4770c1a01b1be1b23772d600b787d411}{go\+R\+U\+Nfrom\+S\+B\+Y} ()
\item 
void \hyperlink{main6_b_8cpp_a300391508ed006e4cd4ee0f9f316f3b4}{go\+R\+U\+Nfrom\+I\+D\+L} ()
\item 
void \hyperlink{main6_b_8cpp_a646dbe8155e1ee44efac5d50a7de878e}{go\+S\+B\+Y} ()
\item 
void \hyperlink{main6_b_8cpp_ae0ed43b60101aed3be6bea960293275d}{go\+S\+B\+Yfrom\+F\+I\+R} ()
\item 
void \hyperlink{main6_b_8cpp_a2d0b911e7b667c6a18000005acb28777}{go\+S\+B\+Yfrom\+R\+U\+N} ()
\item 
void \hyperlink{main6_b_8cpp_a37a57a2b0feb89b22b270931ae440c35}{go\+S\+B\+Yfrom\+I\+D\+L} ()
\item 
void \hyperlink{main6_b_8cpp_aa8d8f1cf694be5de1ac89b91627c0f51}{go\+I\+D\+L} ()
\item 
void \hyperlink{main6_b_8cpp_a3e3cc85ab7a91d6808984a0f78a5f9f8}{go\+I\+D\+Lfrom\+S\+B\+Y} ()
\item 
void \hyperlink{main6_b_8cpp_a690d16feac877ce7000b00e151dffd82}{go\+I\+D\+Lfrom\+R\+U\+N} ()
\item 
void \hyperlink{main6_b_8cpp_ae5438692f2a6c279129ecc19a91568f2}{go\+I\+D\+Lfrom\+F\+I\+R} ()
\item 
void \hyperlink{main6_b_8cpp_a9b07c4b395adfe387d12241e7ebaaae6}{set\+New\+Mode} (string cmd\+Mode\+Request, string \hyperlink{main6_c_8cpp_ab996ab5995af95792f5af3586d943d58}{cmd\+Mode\+Current})
\item 
void \hyperlink{main6_b_8cpp_a5b251dff1da28eda51e8b51bc4b2baf7}{do\+Setup\+I\+O} ()
\end{DoxyCompactItemize}
\subsection*{Variables}
\begin{DoxyCompactItemize}
\item 
char \hyperlink{main6_b_8cpp_a7f7c6b9d49f7b1a42e631ec964d939b9}{id\+C\+U} \mbox{[}80\mbox{]}
\item 
string \hyperlink{main6_b_8cpp_a405cdd34a0ec61abf8c5205c7a8c3182}{cmd\+Version} =\char`\"{}\char`\"{}
\item 
string \hyperlink{main6_b_8cpp_a8a9767341d04352fccd7068bc1d7c370}{cmd\+Mode} =\char`\"{}\char`\"{}
\item 
string \hyperlink{main6_b_8cpp_ab996ab5995af95792f5af3586d943d58}{cmd\+Mode\+Current} =\char`\"{}\char`\"{}
\item 
string \hyperlink{main6_b_8cpp_ad9049cc701250fb177b8e99713039762}{s\+\_\+freq\+T\+P1} =\char`\"{}\char`\"{}
\item 
string \hyperlink{main6_b_8cpp_a396dd1e7a6a9a4dc8b908980e2e1ded4}{s\+\_\+freq\+T\+P2} =\char`\"{}\char`\"{}
\item 
string \hyperlink{main6_b_8cpp_a62d24bc7666ac0bb0d8728dba649a256}{s\+\_\+freq\+T\+P3} =\char`\"{}\char`\"{}
\item 
string \hyperlink{main6_b_8cpp_a6a2b49919f4f32a4af53700ed1cde8ed}{s\+\_\+freq\+T\+P4} =\char`\"{}\char`\"{}
\item 
string \hyperlink{main6_b_8cpp_a4ba85625fa845776a2d64a3f58f36c42}{s\+\_\+count\+Ch1} =\char`\"{}\char`\"{}
\item 
string \hyperlink{main6_b_8cpp_a88730d26d9b63cdf8e4ca277a76b638d}{s\+\_\+count\+Ch2} =\char`\"{}\char`\"{}
\item 
string \hyperlink{main6_b_8cpp_a09052171565a4f15cbfdbc2ebcdd3fff}{s\+\_\+count\+Ch3} =\char`\"{}\char`\"{}
\item 
string \hyperlink{main6_b_8cpp_a32bb7a1f63c92a94ec3d098853bd883b}{s\+\_\+count\+Ch4} =\char`\"{}\char`\"{}
\item 
long \hyperlink{main6_b_8cpp_a7d2353ca53d5b5b259a823a92b7b519e}{freq\+T\+P1} = 10
\item 
long \hyperlink{main6_b_8cpp_a511164d7a4515d9a1f07ccfbda7ea294}{freq\+T\+P2} = 10
\item 
long \hyperlink{main6_b_8cpp_afae1443270cbb13745f612d5425f94a7}{freq\+T\+P3} = 10
\item 
long \hyperlink{main6_b_8cpp_a7cc56f796c77e7b30948d992bacc0429}{freq\+T\+P4} = 10
\item 
long \hyperlink{main6_b_8cpp_a9a1f402dd7e47f25ca3aa9ae7a8d0dc6}{count\+Ch1} = 0
\item 
long \hyperlink{main6_b_8cpp_a49801da896cbdab7c4b39b8e012c1a18}{count\+Ch2} = 0
\item 
long \hyperlink{main6_b_8cpp_a0582794ca95bdcf8787638b7def0177c}{count\+Ch3} = 0
\item 
long \hyperlink{main6_b_8cpp_a1de46864f078711d257187f01dfff541}{count\+Ch4} = 0
\item 
string \hyperlink{main6_b_8cpp_a37ec136ae86c4b7dc81f393bb1a01af7}{s\+\_\+cmd\+P18\+H1} =\char`\"{}\char`\"{}
\item 
string \hyperlink{main6_b_8cpp_a46ce373f60085f5900464cd0731fa20e}{s\+\_\+cmd\+P18\+H2} =\char`\"{}\char`\"{}
\item 
string \hyperlink{main6_b_8cpp_a909acdc96889fb5885793e8bc70b083e}{s\+\_\+cmd\+P18\+H3} =\char`\"{}\char`\"{}
\item 
string \hyperlink{main6_b_8cpp_a607e82175ad61b864bfa84e686437947}{s\+\_\+cmd\+P18\+H4} =\char`\"{}\char`\"{}
\item 
bool \hyperlink{main6_b_8cpp_a1a10d6a42e7c3ba1ad7f396b687a7eb7}{cmd\+P18\+H1}
\item 
bool \hyperlink{main6_b_8cpp_a03df8cc8ee6b4d7ba8a3d2ad50914508}{cmd\+P18\+H2}
\item 
bool \hyperlink{main6_b_8cpp_aba803fecbea259c5af71f0b9f2e9fa5a}{cmd\+P18\+H3}
\item 
bool \hyperlink{main6_b_8cpp_a74d16dd0ede9be1a1645027bd2e6fb21}{cmd\+P18\+H4}
\item 
B\+Y\+T\+E \hyperlink{main6_b_8cpp_a750abfb0120c1735c922980bd47640a5}{buffer} \mbox{[}I2\+C\+\_\+\+M\+A\+X\+\_\+\+B\+U\+F\+\_\+\+S\+I\+Z\+E\mbox{]}
\item 
char \hyperlink{main6_b_8cpp_af54d77a991da4ba360d594c2589140df}{I2\+C\+Input\+Buffer} \mbox{[}I2\+C\+\_\+\+M\+A\+X\+\_\+\+B\+U\+F\+\_\+\+S\+I\+Z\+E\mbox{]}
\item 
char $\ast$ \hyperlink{main6_b_8cpp_abed0c40696905e144ed4118061acf700}{inbuf} = \hyperlink{_v2_01main_8cpp_af54d77a991da4ba360d594c2589140df}{I2\+C\+Input\+Buffer}
\item 
B\+Y\+T\+E \hyperlink{main6_b_8cpp_a92fb5ea5b6a7d108dea33dd07809152d}{address} = \hyperlink{mcatsubsystemconfig_8h_a8fe248bd745b90e2bfe94d8c5fce0a53}{C\+U\+\_\+\+I2\+C\+\_\+\+S\+L\+A\+V\+E\+\_\+\+A\+D\+D\+R}
\item 
B\+Y\+T\+E \hyperlink{main6_b_8cpp_a6c3dedd37414833dd07e72ee4a642d13}{I2\+C\+Stat}
\end{DoxyCompactItemize}

\subsection{Function Documentation}
\hypertarget{main6_b_8cpp_a22bb15ed96d4891d904b55838e451124}{}\index{main6\+B.\+cpp@{main6\+B.\+cpp}!Ascii2\+Byte@{Ascii2\+Byte}}
\index{Ascii2\+Byte@{Ascii2\+Byte}!main6\+B.\+cpp@{main6\+B.\+cpp}}
\subsubsection[{Ascii2\+Byte}]{\setlength{\rightskip}{0pt plus 5cm}B\+Y\+T\+E Ascii2\+Byte (
\begin{DoxyParamCaption}
\item[{char $\ast$}]{buf}
\end{DoxyParamCaption}
)}\label{main6_b_8cpp_a22bb15ed96d4891d904b55838e451124}

Definition at line 1175 of file main6\+B.\+cpp.

\hypertarget{main6_b_8cpp_a2f5a551d47d5257bf34046aede82024e}{}\index{main6\+B.\+cpp@{main6\+B.\+cpp}!control18\+Hmanual@{control18\+Hmanual}}
\index{control18\+Hmanual@{control18\+Hmanual}!main6\+B.\+cpp@{main6\+B.\+cpp}}
\subsubsection[{control18\+Hmanual}]{\setlength{\rightskip}{0pt plus 5cm}void control18\+Hmanual (
\begin{DoxyParamCaption}
\item[{int}]{requested\+Channel, }
\item[{int}]{H\+Flag}
\end{DoxyParamCaption}
)}\label{main6_b_8cpp_a2f5a551d47d5257bf34046aede82024e}

Definition at line 368 of file main6\+B.\+cpp.

\hypertarget{main6_b_8cpp_ae4e046c7843050c83a5f70092acdbe1d}{}\index{main6\+B.\+cpp@{main6\+B.\+cpp}!control18\+L@{control18\+L}}
\index{control18\+L@{control18\+L}!main6\+B.\+cpp@{main6\+B.\+cpp}}
\subsubsection[{control18\+L}]{\setlength{\rightskip}{0pt plus 5cm}void control18\+L (
\begin{DoxyParamCaption}
\item[{int}]{requested\+Channel, }
\item[{int}]{L\+Flag}
\end{DoxyParamCaption}
)}\label{main6_b_8cpp_ae4e046c7843050c83a5f70092acdbe1d}

Definition at line 246 of file main6\+B.\+cpp.

\hypertarget{main6_b_8cpp_acbfa28dfc2a41cc9cea58425f9b75178}{}\index{main6\+B.\+cpp@{main6\+B.\+cpp}!control\+P\+M\+A@{control\+P\+M\+A}}
\index{control\+P\+M\+A@{control\+P\+M\+A}!main6\+B.\+cpp@{main6\+B.\+cpp}}
\subsubsection[{control\+P\+M\+A}]{\setlength{\rightskip}{0pt plus 5cm}void control\+P\+M\+A (
\begin{DoxyParamCaption}
\item[{B\+O\+O\+L}]{P\+M\+Flag}
\end{DoxyParamCaption}
)}\label{main6_b_8cpp_acbfa28dfc2a41cc9cea58425f9b75178}

Definition at line 229 of file main6\+B.\+cpp.

\hypertarget{main6_b_8cpp_a8f5495a6630209795a3fbd7fa61a18e8}{}\index{main6\+B.\+cpp@{main6\+B.\+cpp}!control\+T\+P1@{control\+T\+P1}}
\index{control\+T\+P1@{control\+T\+P1}!main6\+B.\+cpp@{main6\+B.\+cpp}}
\subsubsection[{control\+T\+P1}]{\setlength{\rightskip}{0pt plus 5cm}void control\+T\+P1 (
\begin{DoxyParamCaption}
\item[{B\+O\+O\+L}]{T\+P1\+Flag}
\end{DoxyParamCaption}
)}\label{main6_b_8cpp_a8f5495a6630209795a3fbd7fa61a18e8}
from 5270 code set /// D\+O N\+O\+T U\+S\+E Set\+Intc((long) \&func\+\_\+isr, 19, 1, 1); 

Definition at line 560 of file main6\+B.\+cpp.

\hypertarget{main6_b_8cpp_af2e78c1a970cd9490fcc3a5ac8015e6b}{}\index{main6\+B.\+cpp@{main6\+B.\+cpp}!debug\+Print@{debug\+Print}}
\index{debug\+Print@{debug\+Print}!main6\+B.\+cpp@{main6\+B.\+cpp}}
\subsubsection[{debug\+Print}]{\setlength{\rightskip}{0pt plus 5cm}void debug\+Print (
\begin{DoxyParamCaption}
\item[{string}]{debug\+Msg}
\end{DoxyParamCaption}
)}\label{main6_b_8cpp_af2e78c1a970cd9490fcc3a5ac8015e6b}

Definition at line 154 of file main6\+B.\+cpp.

\hypertarget{main6_b_8cpp_a238885c747f586049b766fa4fcd5ec12}{}\index{main6\+B.\+cpp@{main6\+B.\+cpp}!disable\+All@{disable\+All}}
\index{disable\+All@{disable\+All}!main6\+B.\+cpp@{main6\+B.\+cpp}}
\subsubsection[{disable\+All}]{\setlength{\rightskip}{0pt plus 5cm}void disable\+All (
\begin{DoxyParamCaption}
{}
\end{DoxyParamCaption}
)}\label{main6_b_8cpp_a238885c747f586049b766fa4fcd5ec12}

Definition at line 772 of file main6\+B.\+cpp.

\hypertarget{main6_b_8cpp_a486c7b37eb37847afaeeb6c73de398b9}{}\index{main6\+B.\+cpp@{main6\+B.\+cpp}!display\+Config@{display\+Config}}
\index{display\+Config@{display\+Config}!main6\+B.\+cpp@{main6\+B.\+cpp}}
\subsubsection[{display\+Config}]{\setlength{\rightskip}{0pt plus 5cm}void display\+Config (
\begin{DoxyParamCaption}
{}
\end{DoxyParamCaption}
)}\label{main6_b_8cpp_a486c7b37eb37847afaeeb6c73de398b9}
\hypertarget{main6_b_8cpp_a5b251dff1da28eda51e8b51bc4b2baf7}{}\index{main6\+B.\+cpp@{main6\+B.\+cpp}!do\+Setup\+I\+O@{do\+Setup\+I\+O}}
\index{do\+Setup\+I\+O@{do\+Setup\+I\+O}!main6\+B.\+cpp@{main6\+B.\+cpp}}
\subsubsection[{do\+Setup\+I\+O}]{\setlength{\rightskip}{0pt plus 5cm}void do\+Setup\+I\+O (
\begin{DoxyParamCaption}
{}
\end{DoxyParamCaption}
)}\label{main6_b_8cpp_a5b251dff1da28eda51e8b51bc4b2baf7}

Definition at line 833 of file main6\+B.\+cpp.

\hypertarget{main6_b_8cpp_a0ecec396fb6600a2f4897e7f30318159}{}\index{main6\+B.\+cpp@{main6\+B.\+cpp}!go\+F\+I\+R@{go\+F\+I\+R}}
\index{go\+F\+I\+R@{go\+F\+I\+R}!main6\+B.\+cpp@{main6\+B.\+cpp}}
\subsubsection[{go\+F\+I\+R}]{\setlength{\rightskip}{0pt plus 5cm}void go\+F\+I\+R (
\begin{DoxyParamCaption}
{}
\end{DoxyParamCaption}
)}\label{main6_b_8cpp_a0ecec396fb6600a2f4897e7f30318159}

Definition at line 594 of file main6\+B.\+cpp.

\hypertarget{main6_b_8cpp_affc7dbdeb188c8169ccc6478143538d6}{}\index{main6\+B.\+cpp@{main6\+B.\+cpp}!go\+F\+I\+Rfrom\+I\+D\+L@{go\+F\+I\+Rfrom\+I\+D\+L}}
\index{go\+F\+I\+Rfrom\+I\+D\+L@{go\+F\+I\+Rfrom\+I\+D\+L}!main6\+B.\+cpp@{main6\+B.\+cpp}}
\subsubsection[{go\+F\+I\+Rfrom\+I\+D\+L}]{\setlength{\rightskip}{0pt plus 5cm}void go\+F\+I\+Rfrom\+I\+D\+L (
\begin{DoxyParamCaption}
{}
\end{DoxyParamCaption}
)}\label{main6_b_8cpp_affc7dbdeb188c8169ccc6478143538d6}

Definition at line 628 of file main6\+B.\+cpp.

\hypertarget{main6_b_8cpp_a2d0df7e0313c78e94bb4fafbc5752d67}{}\index{main6\+B.\+cpp@{main6\+B.\+cpp}!go\+F\+I\+Rfrom\+R\+U\+N@{go\+F\+I\+Rfrom\+R\+U\+N}}
\index{go\+F\+I\+Rfrom\+R\+U\+N@{go\+F\+I\+Rfrom\+R\+U\+N}!main6\+B.\+cpp@{main6\+B.\+cpp}}
\subsubsection[{go\+F\+I\+Rfrom\+R\+U\+N}]{\setlength{\rightskip}{0pt plus 5cm}void go\+F\+I\+Rfrom\+R\+U\+N (
\begin{DoxyParamCaption}
{}
\end{DoxyParamCaption}
)}\label{main6_b_8cpp_a2d0df7e0313c78e94bb4fafbc5752d67}

Definition at line 599 of file main6\+B.\+cpp.

\hypertarget{main6_b_8cpp_ae0014243028b5cd808de963c18d01b11}{}\index{main6\+B.\+cpp@{main6\+B.\+cpp}!go\+F\+I\+Rfrom\+S\+B\+Y@{go\+F\+I\+Rfrom\+S\+B\+Y}}
\index{go\+F\+I\+Rfrom\+S\+B\+Y@{go\+F\+I\+Rfrom\+S\+B\+Y}!main6\+B.\+cpp@{main6\+B.\+cpp}}
\subsubsection[{go\+F\+I\+Rfrom\+S\+B\+Y}]{\setlength{\rightskip}{0pt plus 5cm}void go\+F\+I\+Rfrom\+S\+B\+Y (
\begin{DoxyParamCaption}
{}
\end{DoxyParamCaption}
)}\label{main6_b_8cpp_ae0014243028b5cd808de963c18d01b11}

Definition at line 624 of file main6\+B.\+cpp.

\hypertarget{main6_b_8cpp_aa8d8f1cf694be5de1ac89b91627c0f51}{}\index{main6\+B.\+cpp@{main6\+B.\+cpp}!go\+I\+D\+L@{go\+I\+D\+L}}
\index{go\+I\+D\+L@{go\+I\+D\+L}!main6\+B.\+cpp@{main6\+B.\+cpp}}
\subsubsection[{go\+I\+D\+L}]{\setlength{\rightskip}{0pt plus 5cm}void go\+I\+D\+L (
\begin{DoxyParamCaption}
{}
\end{DoxyParamCaption}
)}\label{main6_b_8cpp_aa8d8f1cf694be5de1ac89b91627c0f51}

Definition at line 675 of file main6\+B.\+cpp.

\hypertarget{main6_b_8cpp_ae5438692f2a6c279129ecc19a91568f2}{}\index{main6\+B.\+cpp@{main6\+B.\+cpp}!go\+I\+D\+Lfrom\+F\+I\+R@{go\+I\+D\+Lfrom\+F\+I\+R}}
\index{go\+I\+D\+Lfrom\+F\+I\+R@{go\+I\+D\+Lfrom\+F\+I\+R}!main6\+B.\+cpp@{main6\+B.\+cpp}}
\subsubsection[{go\+I\+D\+Lfrom\+F\+I\+R}]{\setlength{\rightskip}{0pt plus 5cm}void go\+I\+D\+Lfrom\+F\+I\+R (
\begin{DoxyParamCaption}
{}
\end{DoxyParamCaption}
)}\label{main6_b_8cpp_ae5438692f2a6c279129ecc19a91568f2}

Definition at line 688 of file main6\+B.\+cpp.

\hypertarget{main6_b_8cpp_a690d16feac877ce7000b00e151dffd82}{}\index{main6\+B.\+cpp@{main6\+B.\+cpp}!go\+I\+D\+Lfrom\+R\+U\+N@{go\+I\+D\+Lfrom\+R\+U\+N}}
\index{go\+I\+D\+Lfrom\+R\+U\+N@{go\+I\+D\+Lfrom\+R\+U\+N}!main6\+B.\+cpp@{main6\+B.\+cpp}}
\subsubsection[{go\+I\+D\+Lfrom\+R\+U\+N}]{\setlength{\rightskip}{0pt plus 5cm}void go\+I\+D\+Lfrom\+R\+U\+N (
\begin{DoxyParamCaption}
{}
\end{DoxyParamCaption}
)}\label{main6_b_8cpp_a690d16feac877ce7000b00e151dffd82}

Definition at line 684 of file main6\+B.\+cpp.

\hypertarget{main6_b_8cpp_a3e3cc85ab7a91d6808984a0f78a5f9f8}{}\index{main6\+B.\+cpp@{main6\+B.\+cpp}!go\+I\+D\+Lfrom\+S\+B\+Y@{go\+I\+D\+Lfrom\+S\+B\+Y}}
\index{go\+I\+D\+Lfrom\+S\+B\+Y@{go\+I\+D\+Lfrom\+S\+B\+Y}!main6\+B.\+cpp@{main6\+B.\+cpp}}
\subsubsection[{go\+I\+D\+Lfrom\+S\+B\+Y}]{\setlength{\rightskip}{0pt plus 5cm}void go\+I\+D\+Lfrom\+S\+B\+Y (
\begin{DoxyParamCaption}
{}
\end{DoxyParamCaption}
)}\label{main6_b_8cpp_a3e3cc85ab7a91d6808984a0f78a5f9f8}

Definition at line 680 of file main6\+B.\+cpp.

\hypertarget{main6_b_8cpp_af57dea23daabb0f6e6d27f2ef21c9a54}{}\index{main6\+B.\+cpp@{main6\+B.\+cpp}!go\+R\+U\+N@{go\+R\+U\+N}}
\index{go\+R\+U\+N@{go\+R\+U\+N}!main6\+B.\+cpp@{main6\+B.\+cpp}}
\subsubsection[{go\+R\+U\+N}]{\setlength{\rightskip}{0pt plus 5cm}void go\+R\+U\+N (
\begin{DoxyParamCaption}
{}
\end{DoxyParamCaption}
)}\label{main6_b_8cpp_af57dea23daabb0f6e6d27f2ef21c9a54}

Definition at line 633 of file main6\+B.\+cpp.

\hypertarget{main6_b_8cpp_a6d712eb455e679cbf844c6742e7be6a0}{}\index{main6\+B.\+cpp@{main6\+B.\+cpp}!go\+R\+U\+Nfrom\+F\+I\+R@{go\+R\+U\+Nfrom\+F\+I\+R}}
\index{go\+R\+U\+Nfrom\+F\+I\+R@{go\+R\+U\+Nfrom\+F\+I\+R}!main6\+B.\+cpp@{main6\+B.\+cpp}}
\subsubsection[{go\+R\+U\+Nfrom\+F\+I\+R}]{\setlength{\rightskip}{0pt plus 5cm}void go\+R\+U\+Nfrom\+F\+I\+R (
\begin{DoxyParamCaption}
{}
\end{DoxyParamCaption}
)}\label{main6_b_8cpp_a6d712eb455e679cbf844c6742e7be6a0}

Definition at line 644 of file main6\+B.\+cpp.

\hypertarget{main6_b_8cpp_a300391508ed006e4cd4ee0f9f316f3b4}{}\index{main6\+B.\+cpp@{main6\+B.\+cpp}!go\+R\+U\+Nfrom\+I\+D\+L@{go\+R\+U\+Nfrom\+I\+D\+L}}
\index{go\+R\+U\+Nfrom\+I\+D\+L@{go\+R\+U\+Nfrom\+I\+D\+L}!main6\+B.\+cpp@{main6\+B.\+cpp}}
\subsubsection[{go\+R\+U\+Nfrom\+I\+D\+L}]{\setlength{\rightskip}{0pt plus 5cm}void go\+R\+U\+Nfrom\+I\+D\+L (
\begin{DoxyParamCaption}
{}
\end{DoxyParamCaption}
)}\label{main6_b_8cpp_a300391508ed006e4cd4ee0f9f316f3b4}

Definition at line 652 of file main6\+B.\+cpp.

\hypertarget{main6_b_8cpp_a4770c1a01b1be1b23772d600b787d411}{}\index{main6\+B.\+cpp@{main6\+B.\+cpp}!go\+R\+U\+Nfrom\+S\+B\+Y@{go\+R\+U\+Nfrom\+S\+B\+Y}}
\index{go\+R\+U\+Nfrom\+S\+B\+Y@{go\+R\+U\+Nfrom\+S\+B\+Y}!main6\+B.\+cpp@{main6\+B.\+cpp}}
\subsubsection[{go\+R\+U\+Nfrom\+S\+B\+Y}]{\setlength{\rightskip}{0pt plus 5cm}void go\+R\+U\+Nfrom\+S\+B\+Y (
\begin{DoxyParamCaption}
{}
\end{DoxyParamCaption}
)}\label{main6_b_8cpp_a4770c1a01b1be1b23772d600b787d411}

Definition at line 648 of file main6\+B.\+cpp.

\hypertarget{main6_b_8cpp_a646dbe8155e1ee44efac5d50a7de878e}{}\index{main6\+B.\+cpp@{main6\+B.\+cpp}!go\+S\+B\+Y@{go\+S\+B\+Y}}
\index{go\+S\+B\+Y@{go\+S\+B\+Y}!main6\+B.\+cpp@{main6\+B.\+cpp}}
\subsubsection[{go\+S\+B\+Y}]{\setlength{\rightskip}{0pt plus 5cm}void go\+S\+B\+Y (
\begin{DoxyParamCaption}
{}
\end{DoxyParamCaption}
)}\label{main6_b_8cpp_a646dbe8155e1ee44efac5d50a7de878e}

Definition at line 657 of file main6\+B.\+cpp.

\hypertarget{main6_b_8cpp_ae0ed43b60101aed3be6bea960293275d}{}\index{main6\+B.\+cpp@{main6\+B.\+cpp}!go\+S\+B\+Yfrom\+F\+I\+R@{go\+S\+B\+Yfrom\+F\+I\+R}}
\index{go\+S\+B\+Yfrom\+F\+I\+R@{go\+S\+B\+Yfrom\+F\+I\+R}!main6\+B.\+cpp@{main6\+B.\+cpp}}
\subsubsection[{go\+S\+B\+Yfrom\+F\+I\+R}]{\setlength{\rightskip}{0pt plus 5cm}void go\+S\+B\+Yfrom\+F\+I\+R (
\begin{DoxyParamCaption}
{}
\end{DoxyParamCaption}
)}\label{main6_b_8cpp_ae0ed43b60101aed3be6bea960293275d}

Definition at line 662 of file main6\+B.\+cpp.

\hypertarget{main6_b_8cpp_a37a57a2b0feb89b22b270931ae440c35}{}\index{main6\+B.\+cpp@{main6\+B.\+cpp}!go\+S\+B\+Yfrom\+I\+D\+L@{go\+S\+B\+Yfrom\+I\+D\+L}}
\index{go\+S\+B\+Yfrom\+I\+D\+L@{go\+S\+B\+Yfrom\+I\+D\+L}!main6\+B.\+cpp@{main6\+B.\+cpp}}
\subsubsection[{go\+S\+B\+Yfrom\+I\+D\+L}]{\setlength{\rightskip}{0pt plus 5cm}void go\+S\+B\+Yfrom\+I\+D\+L (
\begin{DoxyParamCaption}
{}
\end{DoxyParamCaption}
)}\label{main6_b_8cpp_a37a57a2b0feb89b22b270931ae440c35}

Definition at line 670 of file main6\+B.\+cpp.

\hypertarget{main6_b_8cpp_a2d0b911e7b667c6a18000005acb28777}{}\index{main6\+B.\+cpp@{main6\+B.\+cpp}!go\+S\+B\+Yfrom\+R\+U\+N@{go\+S\+B\+Yfrom\+R\+U\+N}}
\index{go\+S\+B\+Yfrom\+R\+U\+N@{go\+S\+B\+Yfrom\+R\+U\+N}!main6\+B.\+cpp@{main6\+B.\+cpp}}
\subsubsection[{go\+S\+B\+Yfrom\+R\+U\+N}]{\setlength{\rightskip}{0pt plus 5cm}void go\+S\+B\+Yfrom\+R\+U\+N (
\begin{DoxyParamCaption}
{}
\end{DoxyParamCaption}
)}\label{main6_b_8cpp_a2d0b911e7b667c6a18000005acb28777}

Definition at line 666 of file main6\+B.\+cpp.

\hypertarget{main6_b_8cpp_a10570e6420ce0f0a076e1e9d3518d305}{}\index{main6\+B.\+cpp@{main6\+B.\+cpp}!init\+D\+M\+A\+T\+I\+M\+E\+R1@{init\+D\+M\+A\+T\+I\+M\+E\+R1}}
\index{init\+D\+M\+A\+T\+I\+M\+E\+R1@{init\+D\+M\+A\+T\+I\+M\+E\+R1}!main6\+B.\+cpp@{main6\+B.\+cpp}}
\subsubsection[{init\+D\+M\+A\+T\+I\+M\+E\+R1}]{\setlength{\rightskip}{0pt plus 5cm}void init\+D\+M\+A\+T\+I\+M\+E\+R1 (
\begin{DoxyParamCaption}
{}
\end{DoxyParamCaption}
)}\label{main6_b_8cpp_a10570e6420ce0f0a076e1e9d3518d305}
from 5270 code set /// D\+O N\+O\+T U\+S\+E Set\+Intc((long) \&func\+\_\+isr, 19, 1, 1); 

Definition at line 818 of file main6\+B.\+cpp.

\hypertarget{main6_b_8cpp_a89200d64c07024287b4ef31901f44e15}{}\index{main6\+B.\+cpp@{main6\+B.\+cpp}!I\+N\+T\+E\+R\+R\+U\+P\+T@{I\+N\+T\+E\+R\+R\+U\+P\+T}}
\index{I\+N\+T\+E\+R\+R\+U\+P\+T@{I\+N\+T\+E\+R\+R\+U\+P\+T}!main6\+B.\+cpp@{main6\+B.\+cpp}}
\subsubsection[{I\+N\+T\+E\+R\+R\+U\+P\+T}]{\setlength{\rightskip}{0pt plus 5cm}I\+N\+T\+E\+R\+R\+U\+P\+T (
\begin{DoxyParamCaption}
\item[{func\+\_\+isr}]{, }
\item[{0x2600}]{}
\end{DoxyParamCaption}
)}\label{main6_b_8cpp_a89200d64c07024287b4ef31901f44e15}

Definition at line 162 of file main6\+B.\+cpp.

\hypertarget{main6_b_8cpp_ad16e5e62f3579a7048e6b981b172885e}{}\index{main6\+B.\+cpp@{main6\+B.\+cpp}!menu@{menu}}
\index{menu@{menu}!main6\+B.\+cpp@{main6\+B.\+cpp}}
\subsubsection[{menu}]{\setlength{\rightskip}{0pt plus 5cm}void menu (
\begin{DoxyParamCaption}
\item[{void}]{}
\end{DoxyParamCaption}
)}\label{main6_b_8cpp_ad16e5e62f3579a7048e6b981b172885e}

Definition at line 1193 of file main6\+B.\+cpp.

\hypertarget{main6_b_8cpp_ab8ff54f4b027d2dfb6d3b63194fc15a4}{}\index{main6\+B.\+cpp@{main6\+B.\+cpp}!parse\+Block\+C\+U@{parse\+Block\+C\+U}}
\index{parse\+Block\+C\+U@{parse\+Block\+C\+U}!main6\+B.\+cpp@{main6\+B.\+cpp}}
\subsubsection[{parse\+Block\+C\+U}]{\setlength{\rightskip}{0pt plus 5cm}void parse\+Block\+C\+U (
\begin{DoxyParamCaption}
\item[{string}]{Block\+C\+U}
\end{DoxyParamCaption}
)}\label{main6_b_8cpp_ab8ff54f4b027d2dfb6d3b63194fc15a4}

Definition at line 1049 of file main6\+B.\+cpp.

\hypertarget{main6_b_8cpp_aa3032893ba2f121a12d4cecf88277580}{}\index{main6\+B.\+cpp@{main6\+B.\+cpp}!parse\+Block\+G@{parse\+Block\+G}}
\index{parse\+Block\+G@{parse\+Block\+G}!main6\+B.\+cpp@{main6\+B.\+cpp}}
\subsubsection[{parse\+Block\+G}]{\setlength{\rightskip}{0pt plus 5cm}void parse\+Block\+G (
\begin{DoxyParamCaption}
\item[{string}]{Block\+G}
\end{DoxyParamCaption}
)}\label{main6_b_8cpp_aa3032893ba2f121a12d4cecf88277580}

Definition at line 1039 of file main6\+B.\+cpp.

\hypertarget{main6_b_8cpp_a72e39dd7a2538b8b278f927ffd051bde}{}\index{main6\+B.\+cpp@{main6\+B.\+cpp}!parse\+Block\+I\+P\+D@{parse\+Block\+I\+P\+D}}
\index{parse\+Block\+I\+P\+D@{parse\+Block\+I\+P\+D}!main6\+B.\+cpp@{main6\+B.\+cpp}}
\subsubsection[{parse\+Block\+I\+P\+D}]{\setlength{\rightskip}{0pt plus 5cm}void parse\+Block\+I\+P\+D (
\begin{DoxyParamCaption}
\item[{string}]{Block\+I\+P\+D}
\end{DoxyParamCaption}
)}\label{main6_b_8cpp_a72e39dd7a2538b8b278f927ffd051bde}

Definition at line 1060 of file main6\+B.\+cpp.

\hypertarget{main6_b_8cpp_a8109658a433363943c469e7743c238ab}{}\index{main6\+B.\+cpp@{main6\+B.\+cpp}!parse\+Block\+P\+P\+U@{parse\+Block\+P\+P\+U}}
\index{parse\+Block\+P\+P\+U@{parse\+Block\+P\+P\+U}!main6\+B.\+cpp@{main6\+B.\+cpp}}
\subsubsection[{parse\+Block\+P\+P\+U}]{\setlength{\rightskip}{0pt plus 5cm}void parse\+Block\+P\+P\+U (
\begin{DoxyParamCaption}
\item[{string}]{Block\+P\+P\+U}
\end{DoxyParamCaption}
)}\label{main6_b_8cpp_a8109658a433363943c469e7743c238ab}

Definition at line 1115 of file main6\+B.\+cpp.

\hypertarget{main6_b_8cpp_af3350bd69feae78ebcd4f766916eeb67}{}\index{main6\+B.\+cpp@{main6\+B.\+cpp}!parse\+C\+M\+D\+Packet@{parse\+C\+M\+D\+Packet}}
\index{parse\+C\+M\+D\+Packet@{parse\+C\+M\+D\+Packet}!main6\+B.\+cpp@{main6\+B.\+cpp}}
\subsubsection[{parse\+C\+M\+D\+Packet}]{\setlength{\rightskip}{0pt plus 5cm}void parse\+C\+M\+D\+Packet (
\begin{DoxyParamCaption}
\item[{char}]{C\+M\+D\+Packet\mbox{[}\+I2\+C\+\_\+\+M\+A\+X\+\_\+\+B\+U\+F\+\_\+\+S\+I\+Z\+E\mbox{]}}
\end{DoxyParamCaption}
)}\label{main6_b_8cpp_af3350bd69feae78ebcd4f766916eeb67}

Definition at line 894 of file main6\+B.\+cpp.

\hypertarget{main6_b_8cpp_a8a64466bfb43094b3aec845670b959b4}{}\index{main6\+B.\+cpp@{main6\+B.\+cpp}!set\+Defaults@{set\+Defaults}}
\index{set\+Defaults@{set\+Defaults}!main6\+B.\+cpp@{main6\+B.\+cpp}}
\subsubsection[{set\+Defaults}]{\setlength{\rightskip}{0pt plus 5cm}void set\+Defaults (
\begin{DoxyParamCaption}
{}
\end{DoxyParamCaption}
)}\label{main6_b_8cpp_a8a64466bfb43094b3aec845670b959b4}

Definition at line 779 of file main6\+B.\+cpp.

\hypertarget{main6_b_8cpp_a7c3f73193878c079945a21075f128059}{}\index{main6\+B.\+cpp@{main6\+B.\+cpp}!Set\+Intc@{Set\+Intc}}
\index{Set\+Intc@{Set\+Intc}!main6\+B.\+cpp@{main6\+B.\+cpp}}
\subsubsection[{Set\+Intc}]{\setlength{\rightskip}{0pt plus 5cm}void Set\+Intc (
\begin{DoxyParamCaption}
\item[{long}]{func, }
\item[{int}]{vector, }
\item[{int}]{level, }
\item[{int}]{prio}
\end{DoxyParamCaption}
)}\label{main6_b_8cpp_a7c3f73193878c079945a21075f128059}
\hypertarget{main6_b_8cpp_a9b07c4b395adfe387d12241e7ebaaae6}{}\index{main6\+B.\+cpp@{main6\+B.\+cpp}!set\+New\+Mode@{set\+New\+Mode}}
\index{set\+New\+Mode@{set\+New\+Mode}!main6\+B.\+cpp@{main6\+B.\+cpp}}
\subsubsection[{set\+New\+Mode}]{\setlength{\rightskip}{0pt plus 5cm}void set\+New\+Mode (
\begin{DoxyParamCaption}
\item[{string}]{cmd\+Mode\+Request, }
\item[{string}]{cmd\+Mode\+Current}
\end{DoxyParamCaption}
)}\label{main6_b_8cpp_a9b07c4b395adfe387d12241e7ebaaae6}

Definition at line 695 of file main6\+B.\+cpp.

\hypertarget{main6_b_8cpp_a92a0eb6ae19d1612e39cbf1fd318d406}{}\index{main6\+B.\+cpp@{main6\+B.\+cpp}!set\+T\+P1@{set\+T\+P1}}
\index{set\+T\+P1@{set\+T\+P1}!main6\+B.\+cpp@{main6\+B.\+cpp}}
\subsubsection[{set\+T\+P1}]{\setlength{\rightskip}{0pt plus 5cm}void set\+T\+P1 (
\begin{DoxyParamCaption}
\item[{long}]{Frequency}
\end{DoxyParamCaption}
)}\label{main6_b_8cpp_a92a0eb6ae19d1612e39cbf1fd318d406}

Definition at line 539 of file main6\+B.\+cpp.

\hypertarget{main6_b_8cpp_a11ee600b69b27b0bb2d1b5b6e8ece140}{}\index{main6\+B.\+cpp@{main6\+B.\+cpp}!stop\+Pulses@{stop\+Pulses}}
\index{stop\+Pulses@{stop\+Pulses}!main6\+B.\+cpp@{main6\+B.\+cpp}}
\subsubsection[{stop\+Pulses}]{\setlength{\rightskip}{0pt plus 5cm}void stop\+Pulses (
\begin{DoxyParamCaption}
\item[{void $\ast$}]{pdata}
\end{DoxyParamCaption}
)}\label{main6_b_8cpp_a11ee600b69b27b0bb2d1b5b6e8ece140}
\hypertarget{main6_b_8cpp_ace7b2f4c33cbf41f3a43c7be01ff7aec}{}\index{main6\+B.\+cpp@{main6\+B.\+cpp}!User\+Main@{User\+Main}}
\index{User\+Main@{User\+Main}!main6\+B.\+cpp@{main6\+B.\+cpp}}
\subsubsection[{User\+Main}]{\setlength{\rightskip}{0pt plus 5cm}void User\+Main (
\begin{DoxyParamCaption}
\item[{void $\ast$}]{pd}
\end{DoxyParamCaption}
)}\label{main6_b_8cpp_ace7b2f4c33cbf41f3a43c7be01ff7aec}

Definition at line 1224 of file main6\+B.\+cpp.

\subsection{Variable Documentation}
\hypertarget{main6_b_8cpp_a92fb5ea5b6a7d108dea33dd07809152d}{}\index{main6\+B.\+cpp@{main6\+B.\+cpp}!address@{address}}
\index{address@{address}!main6\+B.\+cpp@{main6\+B.\+cpp}}
\subsubsection[{address}]{\setlength{\rightskip}{0pt plus 5cm}B\+Y\+T\+E address = {\bf C\+U\+\_\+\+I2\+C\+\_\+\+S\+L\+A\+V\+E\+\_\+\+A\+D\+D\+R}}\label{main6_b_8cpp_a92fb5ea5b6a7d108dea33dd07809152d}

Definition at line 151 of file main6\+B.\+cpp.

\hypertarget{main6_b_8cpp_a750abfb0120c1735c922980bd47640a5}{}\index{main6\+B.\+cpp@{main6\+B.\+cpp}!buffer@{buffer}}
\index{buffer@{buffer}!main6\+B.\+cpp@{main6\+B.\+cpp}}
\subsubsection[{buffer}]{\setlength{\rightskip}{0pt plus 5cm}B\+Y\+T\+E buffer\mbox{[}I2\+C\+\_\+\+M\+A\+X\+\_\+\+B\+U\+F\+\_\+\+S\+I\+Z\+E\mbox{]}}\label{main6_b_8cpp_a750abfb0120c1735c922980bd47640a5}

Definition at line 148 of file main6\+B.\+cpp.

\hypertarget{main6_b_8cpp_a8a9767341d04352fccd7068bc1d7c370}{}\index{main6\+B.\+cpp@{main6\+B.\+cpp}!cmd\+Mode@{cmd\+Mode}}
\index{cmd\+Mode@{cmd\+Mode}!main6\+B.\+cpp@{main6\+B.\+cpp}}
\subsubsection[{cmd\+Mode}]{\setlength{\rightskip}{0pt plus 5cm}string cmd\+Mode =\char`\"{}\char`\"{}}\label{main6_b_8cpp_a8a9767341d04352fccd7068bc1d7c370}

Definition at line 70 of file main6\+B.\+cpp.

\hypertarget{main6_b_8cpp_ab996ab5995af95792f5af3586d943d58}{}\index{main6\+B.\+cpp@{main6\+B.\+cpp}!cmd\+Mode\+Current@{cmd\+Mode\+Current}}
\index{cmd\+Mode\+Current@{cmd\+Mode\+Current}!main6\+B.\+cpp@{main6\+B.\+cpp}}
\subsubsection[{cmd\+Mode\+Current}]{\setlength{\rightskip}{0pt plus 5cm}string cmd\+Mode\+Current =\char`\"{}\char`\"{}}\label{main6_b_8cpp_ab996ab5995af95792f5af3586d943d58}

Definition at line 71 of file main6\+B.\+cpp.

\hypertarget{main6_b_8cpp_a1a10d6a42e7c3ba1ad7f396b687a7eb7}{}\index{main6\+B.\+cpp@{main6\+B.\+cpp}!cmd\+P18\+H1@{cmd\+P18\+H1}}
\index{cmd\+P18\+H1@{cmd\+P18\+H1}!main6\+B.\+cpp@{main6\+B.\+cpp}}
\subsubsection[{cmd\+P18\+H1}]{\setlength{\rightskip}{0pt plus 5cm}bool cmd\+P18\+H1}\label{main6_b_8cpp_a1a10d6a42e7c3ba1ad7f396b687a7eb7}

Definition at line 93 of file main6\+B.\+cpp.

\hypertarget{main6_b_8cpp_a03df8cc8ee6b4d7ba8a3d2ad50914508}{}\index{main6\+B.\+cpp@{main6\+B.\+cpp}!cmd\+P18\+H2@{cmd\+P18\+H2}}
\index{cmd\+P18\+H2@{cmd\+P18\+H2}!main6\+B.\+cpp@{main6\+B.\+cpp}}
\subsubsection[{cmd\+P18\+H2}]{\setlength{\rightskip}{0pt plus 5cm}bool cmd\+P18\+H2}\label{main6_b_8cpp_a03df8cc8ee6b4d7ba8a3d2ad50914508}

Definition at line 93 of file main6\+B.\+cpp.

\hypertarget{main6_b_8cpp_aba803fecbea259c5af71f0b9f2e9fa5a}{}\index{main6\+B.\+cpp@{main6\+B.\+cpp}!cmd\+P18\+H3@{cmd\+P18\+H3}}
\index{cmd\+P18\+H3@{cmd\+P18\+H3}!main6\+B.\+cpp@{main6\+B.\+cpp}}
\subsubsection[{cmd\+P18\+H3}]{\setlength{\rightskip}{0pt plus 5cm}bool cmd\+P18\+H3}\label{main6_b_8cpp_aba803fecbea259c5af71f0b9f2e9fa5a}

Definition at line 93 of file main6\+B.\+cpp.

\hypertarget{main6_b_8cpp_a74d16dd0ede9be1a1645027bd2e6fb21}{}\index{main6\+B.\+cpp@{main6\+B.\+cpp}!cmd\+P18\+H4@{cmd\+P18\+H4}}
\index{cmd\+P18\+H4@{cmd\+P18\+H4}!main6\+B.\+cpp@{main6\+B.\+cpp}}
\subsubsection[{cmd\+P18\+H4}]{\setlength{\rightskip}{0pt plus 5cm}bool cmd\+P18\+H4}\label{main6_b_8cpp_a74d16dd0ede9be1a1645027bd2e6fb21}

Definition at line 93 of file main6\+B.\+cpp.

\hypertarget{main6_b_8cpp_a405cdd34a0ec61abf8c5205c7a8c3182}{}\index{main6\+B.\+cpp@{main6\+B.\+cpp}!cmd\+Version@{cmd\+Version}}
\index{cmd\+Version@{cmd\+Version}!main6\+B.\+cpp@{main6\+B.\+cpp}}
\subsubsection[{cmd\+Version}]{\setlength{\rightskip}{0pt plus 5cm}string cmd\+Version =\char`\"{}\char`\"{}}\label{main6_b_8cpp_a405cdd34a0ec61abf8c5205c7a8c3182}

Definition at line 69 of file main6\+B.\+cpp.

\hypertarget{main6_b_8cpp_a9a1f402dd7e47f25ca3aa9ae7a8d0dc6}{}\index{main6\+B.\+cpp@{main6\+B.\+cpp}!count\+Ch1@{count\+Ch1}}
\index{count\+Ch1@{count\+Ch1}!main6\+B.\+cpp@{main6\+B.\+cpp}}
\subsubsection[{count\+Ch1}]{\setlength{\rightskip}{0pt plus 5cm}long count\+Ch1 = 0}\label{main6_b_8cpp_a9a1f402dd7e47f25ca3aa9ae7a8d0dc6}

Definition at line 85 of file main6\+B.\+cpp.

\hypertarget{main6_b_8cpp_a49801da896cbdab7c4b39b8e012c1a18}{}\index{main6\+B.\+cpp@{main6\+B.\+cpp}!count\+Ch2@{count\+Ch2}}
\index{count\+Ch2@{count\+Ch2}!main6\+B.\+cpp@{main6\+B.\+cpp}}
\subsubsection[{count\+Ch2}]{\setlength{\rightskip}{0pt plus 5cm}long count\+Ch2 = 0}\label{main6_b_8cpp_a49801da896cbdab7c4b39b8e012c1a18}

Definition at line 86 of file main6\+B.\+cpp.

\hypertarget{main6_b_8cpp_a0582794ca95bdcf8787638b7def0177c}{}\index{main6\+B.\+cpp@{main6\+B.\+cpp}!count\+Ch3@{count\+Ch3}}
\index{count\+Ch3@{count\+Ch3}!main6\+B.\+cpp@{main6\+B.\+cpp}}
\subsubsection[{count\+Ch3}]{\setlength{\rightskip}{0pt plus 5cm}long count\+Ch3 = 0}\label{main6_b_8cpp_a0582794ca95bdcf8787638b7def0177c}

Definition at line 87 of file main6\+B.\+cpp.

\hypertarget{main6_b_8cpp_a1de46864f078711d257187f01dfff541}{}\index{main6\+B.\+cpp@{main6\+B.\+cpp}!count\+Ch4@{count\+Ch4}}
\index{count\+Ch4@{count\+Ch4}!main6\+B.\+cpp@{main6\+B.\+cpp}}
\subsubsection[{count\+Ch4}]{\setlength{\rightskip}{0pt plus 5cm}long count\+Ch4 = 0}\label{main6_b_8cpp_a1de46864f078711d257187f01dfff541}

Definition at line 88 of file main6\+B.\+cpp.

\hypertarget{main6_b_8cpp_a7d2353ca53d5b5b259a823a92b7b519e}{}\index{main6\+B.\+cpp@{main6\+B.\+cpp}!freq\+T\+P1@{freq\+T\+P1}}
\index{freq\+T\+P1@{freq\+T\+P1}!main6\+B.\+cpp@{main6\+B.\+cpp}}
\subsubsection[{freq\+T\+P1}]{\setlength{\rightskip}{0pt plus 5cm}long freq\+T\+P1 = 10}\label{main6_b_8cpp_a7d2353ca53d5b5b259a823a92b7b519e}

Definition at line 81 of file main6\+B.\+cpp.

\hypertarget{main6_b_8cpp_a511164d7a4515d9a1f07ccfbda7ea294}{}\index{main6\+B.\+cpp@{main6\+B.\+cpp}!freq\+T\+P2@{freq\+T\+P2}}
\index{freq\+T\+P2@{freq\+T\+P2}!main6\+B.\+cpp@{main6\+B.\+cpp}}
\subsubsection[{freq\+T\+P2}]{\setlength{\rightskip}{0pt plus 5cm}long freq\+T\+P2 = 10}\label{main6_b_8cpp_a511164d7a4515d9a1f07ccfbda7ea294}

Definition at line 82 of file main6\+B.\+cpp.

\hypertarget{main6_b_8cpp_afae1443270cbb13745f612d5425f94a7}{}\index{main6\+B.\+cpp@{main6\+B.\+cpp}!freq\+T\+P3@{freq\+T\+P3}}
\index{freq\+T\+P3@{freq\+T\+P3}!main6\+B.\+cpp@{main6\+B.\+cpp}}
\subsubsection[{freq\+T\+P3}]{\setlength{\rightskip}{0pt plus 5cm}long freq\+T\+P3 = 10}\label{main6_b_8cpp_afae1443270cbb13745f612d5425f94a7}

Definition at line 83 of file main6\+B.\+cpp.

\hypertarget{main6_b_8cpp_a7cc56f796c77e7b30948d992bacc0429}{}\index{main6\+B.\+cpp@{main6\+B.\+cpp}!freq\+T\+P4@{freq\+T\+P4}}
\index{freq\+T\+P4@{freq\+T\+P4}!main6\+B.\+cpp@{main6\+B.\+cpp}}
\subsubsection[{freq\+T\+P4}]{\setlength{\rightskip}{0pt plus 5cm}long freq\+T\+P4 = 10}\label{main6_b_8cpp_a7cc56f796c77e7b30948d992bacc0429}

Definition at line 84 of file main6\+B.\+cpp.

\hypertarget{main6_b_8cpp_af54d77a991da4ba360d594c2589140df}{}\index{main6\+B.\+cpp@{main6\+B.\+cpp}!I2\+C\+Input\+Buffer@{I2\+C\+Input\+Buffer}}
\index{I2\+C\+Input\+Buffer@{I2\+C\+Input\+Buffer}!main6\+B.\+cpp@{main6\+B.\+cpp}}
\subsubsection[{I2\+C\+Input\+Buffer}]{\setlength{\rightskip}{0pt plus 5cm}char I2\+C\+Input\+Buffer\mbox{[}I2\+C\+\_\+\+M\+A\+X\+\_\+\+B\+U\+F\+\_\+\+S\+I\+Z\+E\mbox{]}}\label{main6_b_8cpp_af54d77a991da4ba360d594c2589140df}

Definition at line 149 of file main6\+B.\+cpp.

\hypertarget{main6_b_8cpp_a6c3dedd37414833dd07e72ee4a642d13}{}\index{main6\+B.\+cpp@{main6\+B.\+cpp}!I2\+C\+Stat@{I2\+C\+Stat}}
\index{I2\+C\+Stat@{I2\+C\+Stat}!main6\+B.\+cpp@{main6\+B.\+cpp}}
\subsubsection[{I2\+C\+Stat}]{\setlength{\rightskip}{0pt plus 5cm}B\+Y\+T\+E I2\+C\+Stat}\label{main6_b_8cpp_a6c3dedd37414833dd07e72ee4a642d13}

Definition at line 152 of file main6\+B.\+cpp.

\hypertarget{main6_b_8cpp_a7f7c6b9d49f7b1a42e631ec964d939b9}{}\index{main6\+B.\+cpp@{main6\+B.\+cpp}!id\+C\+U@{id\+C\+U}}
\index{id\+C\+U@{id\+C\+U}!main6\+B.\+cpp@{main6\+B.\+cpp}}
\subsubsection[{id\+C\+U}]{\setlength{\rightskip}{0pt plus 5cm}char id\+C\+U\mbox{[}80\mbox{]}}\label{main6_b_8cpp_a7f7c6b9d49f7b1a42e631ec964d939b9}

Definition at line 68 of file main6\+B.\+cpp.

\hypertarget{main6_b_8cpp_abed0c40696905e144ed4118061acf700}{}\index{main6\+B.\+cpp@{main6\+B.\+cpp}!inbuf@{inbuf}}
\index{inbuf@{inbuf}!main6\+B.\+cpp@{main6\+B.\+cpp}}
\subsubsection[{inbuf}]{\setlength{\rightskip}{0pt plus 5cm}char$\ast$ inbuf = {\bf I2\+C\+Input\+Buffer}}\label{main6_b_8cpp_abed0c40696905e144ed4118061acf700}

Definition at line 150 of file main6\+B.\+cpp.

\hypertarget{main6_b_8cpp_a37ec136ae86c4b7dc81f393bb1a01af7}{}\index{main6\+B.\+cpp@{main6\+B.\+cpp}!s\+\_\+cmd\+P18\+H1@{s\+\_\+cmd\+P18\+H1}}
\index{s\+\_\+cmd\+P18\+H1@{s\+\_\+cmd\+P18\+H1}!main6\+B.\+cpp@{main6\+B.\+cpp}}
\subsubsection[{s\+\_\+cmd\+P18\+H1}]{\setlength{\rightskip}{0pt plus 5cm}string s\+\_\+cmd\+P18\+H1 =\char`\"{}\char`\"{}}\label{main6_b_8cpp_a37ec136ae86c4b7dc81f393bb1a01af7}

Definition at line 89 of file main6\+B.\+cpp.

\hypertarget{main6_b_8cpp_a46ce373f60085f5900464cd0731fa20e}{}\index{main6\+B.\+cpp@{main6\+B.\+cpp}!s\+\_\+cmd\+P18\+H2@{s\+\_\+cmd\+P18\+H2}}
\index{s\+\_\+cmd\+P18\+H2@{s\+\_\+cmd\+P18\+H2}!main6\+B.\+cpp@{main6\+B.\+cpp}}
\subsubsection[{s\+\_\+cmd\+P18\+H2}]{\setlength{\rightskip}{0pt plus 5cm}string s\+\_\+cmd\+P18\+H2 =\char`\"{}\char`\"{}}\label{main6_b_8cpp_a46ce373f60085f5900464cd0731fa20e}

Definition at line 90 of file main6\+B.\+cpp.

\hypertarget{main6_b_8cpp_a909acdc96889fb5885793e8bc70b083e}{}\index{main6\+B.\+cpp@{main6\+B.\+cpp}!s\+\_\+cmd\+P18\+H3@{s\+\_\+cmd\+P18\+H3}}
\index{s\+\_\+cmd\+P18\+H3@{s\+\_\+cmd\+P18\+H3}!main6\+B.\+cpp@{main6\+B.\+cpp}}
\subsubsection[{s\+\_\+cmd\+P18\+H3}]{\setlength{\rightskip}{0pt plus 5cm}string s\+\_\+cmd\+P18\+H3 =\char`\"{}\char`\"{}}\label{main6_b_8cpp_a909acdc96889fb5885793e8bc70b083e}

Definition at line 91 of file main6\+B.\+cpp.

\hypertarget{main6_b_8cpp_a607e82175ad61b864bfa84e686437947}{}\index{main6\+B.\+cpp@{main6\+B.\+cpp}!s\+\_\+cmd\+P18\+H4@{s\+\_\+cmd\+P18\+H4}}
\index{s\+\_\+cmd\+P18\+H4@{s\+\_\+cmd\+P18\+H4}!main6\+B.\+cpp@{main6\+B.\+cpp}}
\subsubsection[{s\+\_\+cmd\+P18\+H4}]{\setlength{\rightskip}{0pt plus 5cm}string s\+\_\+cmd\+P18\+H4 =\char`\"{}\char`\"{}}\label{main6_b_8cpp_a607e82175ad61b864bfa84e686437947}

Definition at line 92 of file main6\+B.\+cpp.

\hypertarget{main6_b_8cpp_a4ba85625fa845776a2d64a3f58f36c42}{}\index{main6\+B.\+cpp@{main6\+B.\+cpp}!s\+\_\+count\+Ch1@{s\+\_\+count\+Ch1}}
\index{s\+\_\+count\+Ch1@{s\+\_\+count\+Ch1}!main6\+B.\+cpp@{main6\+B.\+cpp}}
\subsubsection[{s\+\_\+count\+Ch1}]{\setlength{\rightskip}{0pt plus 5cm}string s\+\_\+count\+Ch1 =\char`\"{}\char`\"{}}\label{main6_b_8cpp_a4ba85625fa845776a2d64a3f58f36c42}

Definition at line 76 of file main6\+B.\+cpp.

\hypertarget{main6_b_8cpp_a88730d26d9b63cdf8e4ca277a76b638d}{}\index{main6\+B.\+cpp@{main6\+B.\+cpp}!s\+\_\+count\+Ch2@{s\+\_\+count\+Ch2}}
\index{s\+\_\+count\+Ch2@{s\+\_\+count\+Ch2}!main6\+B.\+cpp@{main6\+B.\+cpp}}
\subsubsection[{s\+\_\+count\+Ch2}]{\setlength{\rightskip}{0pt plus 5cm}string s\+\_\+count\+Ch2 =\char`\"{}\char`\"{}}\label{main6_b_8cpp_a88730d26d9b63cdf8e4ca277a76b638d}

Definition at line 77 of file main6\+B.\+cpp.

\hypertarget{main6_b_8cpp_a09052171565a4f15cbfdbc2ebcdd3fff}{}\index{main6\+B.\+cpp@{main6\+B.\+cpp}!s\+\_\+count\+Ch3@{s\+\_\+count\+Ch3}}
\index{s\+\_\+count\+Ch3@{s\+\_\+count\+Ch3}!main6\+B.\+cpp@{main6\+B.\+cpp}}
\subsubsection[{s\+\_\+count\+Ch3}]{\setlength{\rightskip}{0pt plus 5cm}string s\+\_\+count\+Ch3 =\char`\"{}\char`\"{}}\label{main6_b_8cpp_a09052171565a4f15cbfdbc2ebcdd3fff}

Definition at line 78 of file main6\+B.\+cpp.

\hypertarget{main6_b_8cpp_a32bb7a1f63c92a94ec3d098853bd883b}{}\index{main6\+B.\+cpp@{main6\+B.\+cpp}!s\+\_\+count\+Ch4@{s\+\_\+count\+Ch4}}
\index{s\+\_\+count\+Ch4@{s\+\_\+count\+Ch4}!main6\+B.\+cpp@{main6\+B.\+cpp}}
\subsubsection[{s\+\_\+count\+Ch4}]{\setlength{\rightskip}{0pt plus 5cm}string s\+\_\+count\+Ch4 =\char`\"{}\char`\"{}}\label{main6_b_8cpp_a32bb7a1f63c92a94ec3d098853bd883b}

Definition at line 79 of file main6\+B.\+cpp.

\hypertarget{main6_b_8cpp_ad9049cc701250fb177b8e99713039762}{}\index{main6\+B.\+cpp@{main6\+B.\+cpp}!s\+\_\+freq\+T\+P1@{s\+\_\+freq\+T\+P1}}
\index{s\+\_\+freq\+T\+P1@{s\+\_\+freq\+T\+P1}!main6\+B.\+cpp@{main6\+B.\+cpp}}
\subsubsection[{s\+\_\+freq\+T\+P1}]{\setlength{\rightskip}{0pt plus 5cm}string s\+\_\+freq\+T\+P1 =\char`\"{}\char`\"{}}\label{main6_b_8cpp_ad9049cc701250fb177b8e99713039762}

Definition at line 72 of file main6\+B.\+cpp.

\hypertarget{main6_b_8cpp_a396dd1e7a6a9a4dc8b908980e2e1ded4}{}\index{main6\+B.\+cpp@{main6\+B.\+cpp}!s\+\_\+freq\+T\+P2@{s\+\_\+freq\+T\+P2}}
\index{s\+\_\+freq\+T\+P2@{s\+\_\+freq\+T\+P2}!main6\+B.\+cpp@{main6\+B.\+cpp}}
\subsubsection[{s\+\_\+freq\+T\+P2}]{\setlength{\rightskip}{0pt plus 5cm}string s\+\_\+freq\+T\+P2 =\char`\"{}\char`\"{}}\label{main6_b_8cpp_a396dd1e7a6a9a4dc8b908980e2e1ded4}

Definition at line 73 of file main6\+B.\+cpp.

\hypertarget{main6_b_8cpp_a62d24bc7666ac0bb0d8728dba649a256}{}\index{main6\+B.\+cpp@{main6\+B.\+cpp}!s\+\_\+freq\+T\+P3@{s\+\_\+freq\+T\+P3}}
\index{s\+\_\+freq\+T\+P3@{s\+\_\+freq\+T\+P3}!main6\+B.\+cpp@{main6\+B.\+cpp}}
\subsubsection[{s\+\_\+freq\+T\+P3}]{\setlength{\rightskip}{0pt plus 5cm}string s\+\_\+freq\+T\+P3 =\char`\"{}\char`\"{}}\label{main6_b_8cpp_a62d24bc7666ac0bb0d8728dba649a256}

Definition at line 74 of file main6\+B.\+cpp.

\hypertarget{main6_b_8cpp_a6a2b49919f4f32a4af53700ed1cde8ed}{}\index{main6\+B.\+cpp@{main6\+B.\+cpp}!s\+\_\+freq\+T\+P4@{s\+\_\+freq\+T\+P4}}
\index{s\+\_\+freq\+T\+P4@{s\+\_\+freq\+T\+P4}!main6\+B.\+cpp@{main6\+B.\+cpp}}
\subsubsection[{s\+\_\+freq\+T\+P4}]{\setlength{\rightskip}{0pt plus 5cm}string s\+\_\+freq\+T\+P4 =\char`\"{}\char`\"{}}\label{main6_b_8cpp_a6a2b49919f4f32a4af53700ed1cde8ed}

Definition at line 75 of file main6\+B.\+cpp.

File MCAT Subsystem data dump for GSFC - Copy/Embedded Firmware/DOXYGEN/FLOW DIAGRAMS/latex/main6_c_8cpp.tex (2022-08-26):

\hypertarget{main6_c_8cpp}{}\section{C\+:/\+Users/samudra/\+Google Drive/\+M\+C\+A\+T4\+C\+U\+F\+S\+W/main6\+C.cpp File Reference}
\label{main6_c_8cpp}\index{C\+:/\+Users/samudra/\+Google Drive/\+M\+C\+A\+T4\+C\+U\+F\+S\+W/main6\+C.\+cpp@{C\+:/\+Users/samudra/\+Google Drive/\+M\+C\+A\+T4\+C\+U\+F\+S\+W/main6\+C.\+cpp}}
{\ttfamily \#include \char`\"{}predef.\+h\char`\"{}}\\*
{\ttfamily \#include $<$stdio.\+h$>$}\\*
{\ttfamily \#include $<$ctype.\+h$>$}\\*
{\ttfamily \#include $<$startnet.\+h$>$}\\*
{\ttfamily \#include $<$autoupdate.\+h$>$}\\*
{\ttfamily \#include $<$dhcpclient.\+h$>$}\\*
{\ttfamily \#include $<$taskmon.\+h$>$}\\*
{\ttfamily \#include $<$smarttrap.\+h$>$}\\*
{\ttfamily \#include $<$string.\+h$>$}\\*
{\ttfamily \#include $<$math.\+h$>$}\\*
{\ttfamily \#include $<$assert.\+h$>$}\\*
{\ttfamily \#include $<$multichanneli2c.\+h$>$}\\*
{\ttfamily \#include $<$sim5441x.\+h$>$}\\*
{\ttfamily \#include $<$cfinter.\+h$>$}\\*
{\ttfamily \#include $<$iostream$>$}\\*
{\ttfamily \#include $<$iomanip$>$}\\*
{\ttfamily \#include $<$string$>$}\\*
{\ttfamily \#include \char`\"{}mcat\+\_\+config.\+h\char`\"{}}\\*
{\ttfamily \#include \char`\"{}mcat\+\_\+cmd\+\_\+packet.\+h\char`\"{}}\\*
{\ttfamily \#include \char`\"{}mcat\+\_\+timing.\+h\char`\"{}}\\*
{\ttfamily \#include \char`\"{}periph\+\_\+clocks.\+h\char`\"{}}\\*
Include dependency graph for main6\+C.\+cpp\+:
\nopagebreak
\begin{figure}[H]
\begin{center}
\leavevmode
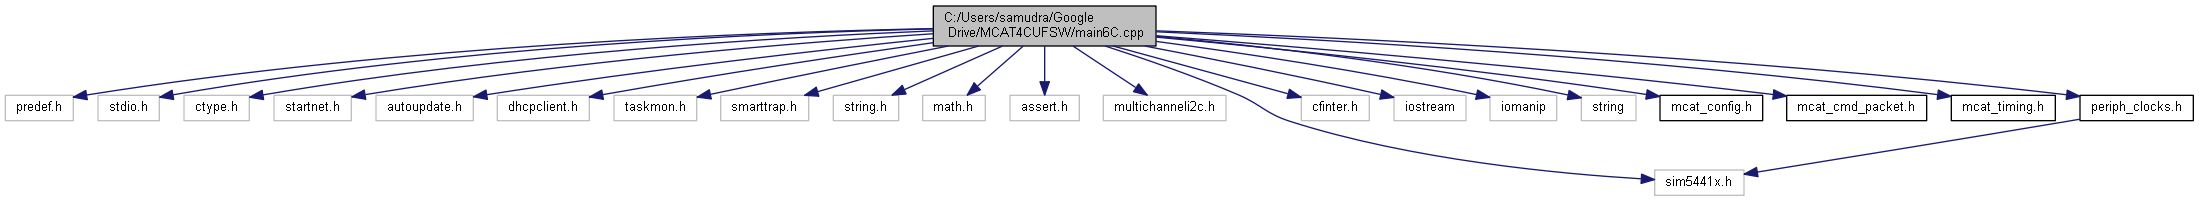
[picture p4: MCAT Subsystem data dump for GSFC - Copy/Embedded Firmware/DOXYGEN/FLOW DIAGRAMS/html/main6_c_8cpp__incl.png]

\end{center}
\end{figure}
\subsection*{Functions}
\begin{DoxyCompactItemize}
\item 
void \hyperlink{main6_c_8cpp_af3350bd69feae78ebcd4f766916eeb67}{parse\+C\+M\+D\+Packet} (char C\+M\+D\+Packet\mbox{[}I2\+C\+\_\+\+M\+A\+X\+\_\+\+B\+U\+F\+\_\+\+S\+I\+Z\+E\mbox{]})
\item 
void \hyperlink{main6_c_8cpp_aa3032893ba2f121a12d4cecf88277580}{parse\+Block\+G} (string Block\+G)
\item 
void \hyperlink{main6_c_8cpp_ab8ff54f4b027d2dfb6d3b63194fc15a4}{parse\+Block\+C\+U} (string Block\+C\+U)
\item 
void \hyperlink{main6_c_8cpp_a72e39dd7a2538b8b278f927ffd051bde}{parse\+Block\+I\+P\+D} (string Block\+I\+P\+D)
\item 
void \hyperlink{main6_c_8cpp_a8109658a433363943c469e7743c238ab}{parse\+Block\+P\+P\+U} (string Block\+P\+P\+U)
\item 
B\+Y\+T\+E \hyperlink{main6_c_8cpp_a22bb15ed96d4891d904b55838e451124}{Ascii2\+Byte} (char $\ast$buf)
\item 
void \hyperlink{main6_c_8cpp_ad16e5e62f3579a7048e6b981b172885e}{menu} (void)
\item 
void \hyperlink{main6_c_8cpp_ace7b2f4c33cbf41f3a43c7be01ff7aec}{User\+Main} (void $\ast$pd)
\item 
void \hyperlink{main6_c_8cpp_a486c7b37eb37847afaeeb6c73de398b9}{display\+Config} ()
\item 
void \hyperlink{main6_c_8cpp_a11ee600b69b27b0bb2d1b5b6e8ece140}{stop\+Pulses} (void $\ast$pdata)
\item 
void \hyperlink{main6_c_8cpp_a10570e6420ce0f0a076e1e9d3518d305}{init\+D\+M\+A\+T\+I\+M\+E\+R1} ()
\item 
void \hyperlink{main6_c_8cpp_a7c3f73193878c079945a21075f128059}{Set\+Intc} (long func, int vector, int level, int prio)
\item 
void \hyperlink{main6_c_8cpp_a8a64466bfb43094b3aec845670b959b4}{set\+Defaults} ()
\item 
void \hyperlink{main6_c_8cpp_a238885c747f586049b766fa4fcd5ec12}{disable\+All} ()
\item 
void \hyperlink{main6_c_8cpp_af2e78c1a970cd9490fcc3a5ac8015e6b}{debug\+Print} (string debug\+Msg)
\item 
\hyperlink{main6_c_8cpp_a89200d64c07024287b4ef31901f44e15}{I\+N\+T\+E\+R\+R\+U\+P\+T} (func\+\_\+isr, 0x2600)
\item 
void \hyperlink{main6_c_8cpp_acbfa28dfc2a41cc9cea58425f9b75178}{control\+P\+M\+A} (B\+O\+O\+L P\+M\+Flag)
\item 
void \hyperlink{main6_c_8cpp_ae4e046c7843050c83a5f70092acdbe1d}{control18\+L} (int requested\+Channel, int L\+Flag)
\item 
void \hyperlink{main6_c_8cpp_a2f5a551d47d5257bf34046aede82024e}{control18\+Hmanual} (int requested\+Channel, int H\+Flag)
\item 
void \hyperlink{main6_c_8cpp_a92a0eb6ae19d1612e39cbf1fd318d406}{set\+T\+P1} (long Frequency)
\item 
void \hyperlink{main6_c_8cpp_a8f5495a6630209795a3fbd7fa61a18e8}{control\+T\+P1} (B\+O\+O\+L T\+P1\+Flag)
\item 
void \hyperlink{main6_c_8cpp_a0ecec396fb6600a2f4897e7f30318159}{go\+F\+I\+R} ()
\item 
void \hyperlink{main6_c_8cpp_a2d0df7e0313c78e94bb4fafbc5752d67}{go\+F\+I\+Rfrom\+R\+U\+N} ()
\item 
void \hyperlink{main6_c_8cpp_ae0014243028b5cd808de963c18d01b11}{go\+F\+I\+Rfrom\+S\+B\+Y} ()
\item 
void \hyperlink{main6_c_8cpp_affc7dbdeb188c8169ccc6478143538d6}{go\+F\+I\+Rfrom\+I\+D\+L} ()
\item 
void \hyperlink{main6_c_8cpp_af57dea23daabb0f6e6d27f2ef21c9a54}{go\+R\+U\+N} ()
\item 
void \hyperlink{main6_c_8cpp_a6d712eb455e679cbf844c6742e7be6a0}{go\+R\+U\+Nfrom\+F\+I\+R} ()
\item 
void \hyperlink{main6_c_8cpp_a4770c1a01b1be1b23772d600b787d411}{go\+R\+U\+Nfrom\+S\+B\+Y} ()
\item 
void \hyperlink{main6_c_8cpp_a300391508ed006e4cd4ee0f9f316f3b4}{go\+R\+U\+Nfrom\+I\+D\+L} ()
\item 
void \hyperlink{main6_c_8cpp_a646dbe8155e1ee44efac5d50a7de878e}{go\+S\+B\+Y} ()
\item 
void \hyperlink{main6_c_8cpp_ae0ed43b60101aed3be6bea960293275d}{go\+S\+B\+Yfrom\+F\+I\+R} ()
\item 
void \hyperlink{main6_c_8cpp_a2d0b911e7b667c6a18000005acb28777}{go\+S\+B\+Yfrom\+R\+U\+N} ()
\item 
void \hyperlink{main6_c_8cpp_a37a57a2b0feb89b22b270931ae440c35}{go\+S\+B\+Yfrom\+I\+D\+L} ()
\item 
void \hyperlink{main6_c_8cpp_aa8d8f1cf694be5de1ac89b91627c0f51}{go\+I\+D\+L} ()
\item 
void \hyperlink{main6_c_8cpp_a3e3cc85ab7a91d6808984a0f78a5f9f8}{go\+I\+D\+Lfrom\+S\+B\+Y} ()
\item 
void \hyperlink{main6_c_8cpp_a690d16feac877ce7000b00e151dffd82}{go\+I\+D\+Lfrom\+R\+U\+N} ()
\item 
void \hyperlink{main6_c_8cpp_ae5438692f2a6c279129ecc19a91568f2}{go\+I\+D\+Lfrom\+F\+I\+R} ()
\item 
void \hyperlink{main6_c_8cpp_a9b07c4b395adfe387d12241e7ebaaae6}{set\+New\+Mode} (string cmd\+Mode\+Request, string \hyperlink{main6_c_8cpp_ab996ab5995af95792f5af3586d943d58}{cmd\+Mode\+Current})
\item 
void \hyperlink{main6_c_8cpp_ab482d6ef2e62e38354a2ab1d1e9827d3}{do\+Setup} ()
\item 
void \hyperlink{main6_c_8cpp_ae545852079ad06cd4f5cd017dd5c8249}{set\+New\+Pulse\+Count} ()
\item 
void \hyperlink{main6_c_8cpp_a8cbbd11ea6ebd5f8ad4a432646a65267}{disable\+Peripherals} ()
\end{DoxyCompactItemize}
\subsection*{Variables}
\begin{DoxyCompactItemize}
\item 
D\+W\+O\+R\+D \hyperlink{main6_c_8cpp_a1a81dd9879f21195e8d3b4d471524ccb}{start\+Pulse\+Count}
\item 
D\+W\+O\+R\+D \hyperlink{main6_c_8cpp_a694b66dde3c298b6b234344941a64bb9}{end\+Pulse\+Count}
\item 
B\+O\+O\+L \hyperlink{main6_c_8cpp_a5cbcba8bebc277fc9c0be941fdb92e82}{toggle\+H\+Flag}
\item 
char \hyperlink{main6_c_8cpp_a67cb76a345ef77fbb558f70971b6dc92}{id\+Q} \mbox{[}80\mbox{]}
\item 
char \hyperlink{main6_c_8cpp_a2dfc1feb8ca92d02b052fcb15b378560}{id\+C\+U} \mbox{[}160\mbox{]}
\item 
char \hyperlink{main6_c_8cpp_a9fbcbc3382bca9c438e08a693bc0369e}{ver\+C\+U} \mbox{[}2\mbox{]}
\item 
string \hyperlink{main6_c_8cpp_a405cdd34a0ec61abf8c5205c7a8c3182}{cmd\+Version} =\char`\"{}\char`\"{}
\item 
string \hyperlink{main6_c_8cpp_a8a9767341d04352fccd7068bc1d7c370}{cmd\+Mode} =\char`\"{}\char`\"{}
\item 
string \hyperlink{main6_c_8cpp_ab996ab5995af95792f5af3586d943d58}{cmd\+Mode\+Current} =\char`\"{}\char`\"{}
\item 
string \hyperlink{main6_c_8cpp_ad9049cc701250fb177b8e99713039762}{s\+\_\+freq\+T\+P1} =\char`\"{}\char`\"{}
\item 
string \hyperlink{main6_c_8cpp_a396dd1e7a6a9a4dc8b908980e2e1ded4}{s\+\_\+freq\+T\+P2} =\char`\"{}\char`\"{}
\item 
string \hyperlink{main6_c_8cpp_a62d24bc7666ac0bb0d8728dba649a256}{s\+\_\+freq\+T\+P3} =\char`\"{}\char`\"{}
\item 
string \hyperlink{main6_c_8cpp_a6a2b49919f4f32a4af53700ed1cde8ed}{s\+\_\+freq\+T\+P4} =\char`\"{}\char`\"{}
\item 
string \hyperlink{main6_c_8cpp_a4ba85625fa845776a2d64a3f58f36c42}{s\+\_\+count\+Ch1} =\char`\"{}\char`\"{}
\item 
string \hyperlink{main6_c_8cpp_a88730d26d9b63cdf8e4ca277a76b638d}{s\+\_\+count\+Ch2} =\char`\"{}\char`\"{}
\item 
string \hyperlink{main6_c_8cpp_a09052171565a4f15cbfdbc2ebcdd3fff}{s\+\_\+count\+Ch3} =\char`\"{}\char`\"{}
\item 
string \hyperlink{main6_c_8cpp_a32bb7a1f63c92a94ec3d098853bd883b}{s\+\_\+count\+Ch4} =\char`\"{}\char`\"{}
\item 
long \hyperlink{main6_c_8cpp_a7d2353ca53d5b5b259a823a92b7b519e}{freq\+T\+P1} = 10
\item 
long \hyperlink{main6_c_8cpp_a511164d7a4515d9a1f07ccfbda7ea294}{freq\+T\+P2} = 10
\item 
long \hyperlink{main6_c_8cpp_afae1443270cbb13745f612d5425f94a7}{freq\+T\+P3} = 10
\item 
long \hyperlink{main6_c_8cpp_a7cc56f796c77e7b30948d992bacc0429}{freq\+T\+P4} = 10
\item 
long \hyperlink{main6_c_8cpp_a9a1f402dd7e47f25ca3aa9ae7a8d0dc6}{count\+Ch1} = 0
\item 
long \hyperlink{main6_c_8cpp_a49801da896cbdab7c4b39b8e012c1a18}{count\+Ch2} = 0
\item 
long \hyperlink{main6_c_8cpp_a0582794ca95bdcf8787638b7def0177c}{count\+Ch3} = 0
\item 
long \hyperlink{main6_c_8cpp_a1de46864f078711d257187f01dfff541}{count\+Ch4} = 0
\item 
string \hyperlink{main6_c_8cpp_a37ec136ae86c4b7dc81f393bb1a01af7}{s\+\_\+cmd\+P18\+H1} =\char`\"{}\char`\"{}
\item 
string \hyperlink{main6_c_8cpp_a46ce373f60085f5900464cd0731fa20e}{s\+\_\+cmd\+P18\+H2} =\char`\"{}\char`\"{}
\item 
string \hyperlink{main6_c_8cpp_a909acdc96889fb5885793e8bc70b083e}{s\+\_\+cmd\+P18\+H3} =\char`\"{}\char`\"{}
\item 
string \hyperlink{main6_c_8cpp_a607e82175ad61b864bfa84e686437947}{s\+\_\+cmd\+P18\+H4} =\char`\"{}\char`\"{}
\item 
bool \hyperlink{main6_c_8cpp_a1a10d6a42e7c3ba1ad7f396b687a7eb7}{cmd\+P18\+H1}
\item 
bool \hyperlink{main6_c_8cpp_a03df8cc8ee6b4d7ba8a3d2ad50914508}{cmd\+P18\+H2}
\item 
bool \hyperlink{main6_c_8cpp_aba803fecbea259c5af71f0b9f2e9fa5a}{cmd\+P18\+H3}
\item 
bool \hyperlink{main6_c_8cpp_a74d16dd0ede9be1a1645027bd2e6fb21}{cmd\+P18\+H4}
\item 
B\+Y\+T\+E \hyperlink{main6_c_8cpp_a750abfb0120c1735c922980bd47640a5}{buffer} \mbox{[}I2\+C\+\_\+\+M\+A\+X\+\_\+\+B\+U\+F\+\_\+\+S\+I\+Z\+E\mbox{]}
\item
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

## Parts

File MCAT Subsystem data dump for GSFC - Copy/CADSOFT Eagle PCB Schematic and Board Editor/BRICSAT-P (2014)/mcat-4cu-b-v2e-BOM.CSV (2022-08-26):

Part | Value | Device | Package | Description | MF | MPN | OC_FARNELL
C1 | 68uF | OSCON-50SVPF68M | OS-CON-SVPF-F12
C2 | 4.7uF | AVX-LD105C475KAB2A | MLCC-X7R-1210
C3 | 10uF | C-USC1210K | C1210K | CAPACITOR, American symbol
C4 | 10uF | C-USC1210K | C1210K | CAPACITOR, American symbol
C5 | 68uF | OSCON-50SVPF68M | OS-CON-SVPF-F12
H1 | MOUNT-PAD-ROUNDCSK_MTG_HOLE_A5 | MOUNT-PAD-ROUNDCSK_MTG_HOLE_A5 | CSK_MOUNTING_HOLE | MOUNTING PAD, round
H2 | MOUNT-PAD-ROUNDCSK_MTG_HOLE_A5 | MOUNT-PAD-ROUNDCSK_MTG_HOLE_A5 | CSK_MOUNTING_HOLE | MOUNTING PAD, round
H3 | MOUNT-PAD-ROUNDCSK_MTG_HOLE_A5 | MOUNT-PAD-ROUNDCSK_MTG_HOLE_A5 | CSK_MOUNTING_HOLE | MOUNTING PAD, round
HBL | MOUNT-PAD-ROUNDCSK_MTG_HOLE_A5 | MOUNT-PAD-ROUNDCSK_MTG_HOLE_A5 | CSK_MOUNTING_HOLE | MOUNTING PAD, round
J1 | 2 x ESQ-126-39-G-D | CSK-BUS-CONN2X2X26 | CSK-BUS-PKG | Cubesat Kit Bus Connector
J2 | M80-6810642 | M80-6810642 | M80-68106
J3 | AMPMODU 5X2 SMT HDR | AMPMODU-5-146131-X(5X2) | AMPMODU-SMT-PIN-HEADER-5X2
J4 | M80-6811242 | M80-6811242 | M80-68112
J5 | M80-6811242 | M80-6811242 | M80-68112
L1 | 33 uH | MSS1038-333ML_ | MSS1048
L2 | 330 uH | MSS1048-334KL_ | MSS1048
L3 | 10 uH | ELL-5PS100M | SERIES-POWER-INDUCTORS |  | PANASONIC | ELL5PS100M | 1717452
OK1 | PS2501L-4 | PS2501L-4 | PS2501L-4
OK2 | PS2501L-4 | PS2501L-4 | PS2501L-4
OK3 | PS2501L-4 | PS2501L-4 | PS2501L-4
Q1 | SI5404BDC | SI5404BDC | 1206-8-CHIPFET
Q2 | SI5404BDC | SI5404BDC | 1206-8-CHIPFET
Q3 | SI5404BDC | SI5404BDC | 1206-8-CHIPFET
Q4 | SI5404BDC | SI5404BDC | 1206-8-CHIPFET
Q5 | SI5404BDC | SI5404BDC | 1206-8-CHIPFET
Q6 | SI5404BDC | SI5404BDC | 1206-8-CHIPFET
Q7 | SI5404BDC | SI5404BDC | 1206-8-CHIPFET
Q8 | SI5404BDC | SI5404BDC | 1206-8-CHIPFET
R1 | 3K79 | R-US_R0805 | R0805 | RESISTOR, American symbol
R2 | 1K | R-US_R0805 | R0805 | RESISTOR, American symbol
R3 | 70 mOhms | R-US_R1206 | R1206 | RESISTOR, American symbol
R4 | 4k7 0.1% | R-US_R0603 | R0603 | RESISTOR, American symbol
R5 | 1K | R-US_R0805 | R0805 | RESISTOR, American symbol
R6 | 604R | R-US_R0805 | R0805 | RESISTOR, American symbol
R7 | 5K42 | R-US_R1206 | R1206 | RESISTOR, American symbol
R8 | 5K42 | R-US_R1206 | R1206 | RESISTOR, American symbol
R9 | 5K42 | R-US_R1206 | R1206 | RESISTOR, American symbol
R10 | 5K42 | R-US_R1206 | R1206 | RESISTOR, American symbol
R11 | 5K42 | R-US_R1206 | R1206 | RESISTOR, American symbol
R12 | 5K42 | R-US_R1206 | R1206 | RESISTOR, American symbol
R13 | 5K42 0.1% | R-US_R1206 | R1206 | RESISTOR, American symbol
R14 | 5K42 0.1% | R-US_R1206 | R1206 | RESISTOR, American symbol
R15 | R-US_R0402 | R-US_R0402 | R0402 | RESISTOR, American symbol
R16 | 100K 0.1% | R-US_R0402 | R0402 | RESISTOR, American symbol
R17 | 100K 0.1% | R-US_R0402 | R0402 | RESISTOR, American symbol
R18 | 100K 0.1% | R-US_R0402 | R0402 | RESISTOR, American symbol
R19 | 100K 0.1% | R-US_R0402 | R0402 | RESISTOR, American symbol
R20 | 100K 0.1% | R-US_R0402 | R0402 | RESISTOR, American symbol
R21 | 100K 0.1% | R-US_R0402 | R0402 | RESISTOR, American symbol
R22 | 100K 0.1% | R-US_R0402 | R0402 | RESISTOR, American symbol
R23 | 51K 0.1% | R-US_R0603 | R0603 | RESISTOR, American symbol
R24 | 51K 0.1% | R-US_R0603 | R0603 | RESISTOR, American symbol
R25 | 51K 0.1% | R-US_R0603 | R0603 | RESISTOR, American symbol
R26 | 51K 0.1% | R-US_R0603 | R0603 | RESISTOR, American symbol
R27 | 51K 0.1% | R-US_R0603 | R0603 | RESISTOR, American symbol
R28 | 51K 0.1% | R-US_R0603 | R0603 | RESISTOR, American symbol
R29 | 51k 0.1% | R-US_R0603 | R0603 | RESISTOR, American symbol
R30 | 51k 0.1% | R-US_R0603 | R0603 | RESISTOR, American symbol
R31 | 0.1R 1% PTC | R-US_R0402 | R0402 | RESISTOR, American symbol
R32 | 0.1R 1% PTC | R-US_R0402 | R0402 | RESISTOR, American symbol
R33 | 0.1R 1% PTC | R-US_R0402 | R0402 | RESISTOR, American symbol
R34 | 0.1R 1% PTC | R-US_R0402 | R0402 | RESISTOR, American symbol
SJ1 | 0R | SJ | SJ | SMD solder JUMPER
SJ2 | 0R | SJ | SJ | SMD solder JUMPER
SJ3 | 0R | SJ | SJ | SMD solder JUMPER
SJ4 | 0R | SJ | SJ | SMD solder JUMPER
U1 | LTM4609MPV#PBF | LTM4609MPV#PBFROHS/HITEMP | LGA-141-LTC-05-08-1840-B | Per LTC Datasheet 4609fe LTM4609 (c) Samudra Haque, N3RDX, 2/23/2014
U2 | UCAT-4CU-B-CONTROL-UNITNANO55415 | UCAT-4CU-B-CONTROL-UNITNANO55415 | MOLEX-MINI-PCI-EXPRESS-8MM-52CKT
U3 | LT1161ISW | LT1161ISW | 20-LEAD-PLASTIC-SO
U4 | LT1161ISW | LT1161ISW | 20-LEAD-PLASTIC-SO

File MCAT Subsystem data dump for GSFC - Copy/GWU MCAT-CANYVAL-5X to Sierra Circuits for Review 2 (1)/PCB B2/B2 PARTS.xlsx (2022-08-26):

Part | Value | Device | Package | Description | COPYRIGHT | MF | MPN | PCBLABEL
~~B3~~ | ~~MCAT-4CU-C-PCB/MID~~ | ~~MCAT-4CU-C-PCB/MID~~ | ~~MCAT-4CU-C-MID-V4-BLANK~~ |  | ~~(c) 2015, GWU~~ |  |  | ~~B2~~
F1 | SMTRAM2-6-5 | SMTRAM2-6-5 | SMTRA-M2-6-5 | Type SMTRA - ReelFast Surface Mount Right Angle (R'ANGLE) Fastener (Metric) |  | Penn Engineering | SMTRAM2-6-5-DT
F7 | SMTRAM2-6-5 | SMTRAM2-6-5 | SMTRA-M2-6-5 | Type SMTRA - ReelFast Surface Mount Right Angle (R'ANGLE) Fastener (Metric) |  | Penn Engineering | SMTRAM2-6-5-DT
~~THL2:TH2~~ | ~~MCAT-TH-G4X-YONSEI/LH~~ | ~~MCAT-TH-G4X-YONSEI/LH~~ | ~~MCAT-TH-G4X-LH~~ | ~~Thruster for CANYVAL bus. Note LH and RH orientations are separate, and opposing pin arrangements. Layers are also flipped.~~
~~THR1:TH2~~ | ~~MCAT-TH-G4X-YONSEI/RH~~ | ~~MCAT-TH-G4X-YONSEI/RH~~ | ~~MCAT-TH-G4X-RH~~ | ~~Thruster for CANYVAL bus. Note LH and RH orientations are separate, and opposing pin arrangements. Layers are also flipped.~~

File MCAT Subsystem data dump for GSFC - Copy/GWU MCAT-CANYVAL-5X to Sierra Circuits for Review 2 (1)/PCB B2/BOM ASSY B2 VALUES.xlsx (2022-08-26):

George Washington University
BOM: | B2 | REV: | 5X
Date | 2015-03-04
Item# | Install? | Qty | Parts | Value | Package/footprint | Distributor | Distributor P/N | Manufacturer | Manufacturer P/N | Device | Description
1 | DNI | 1 | THL2:TH2 | MCAT-TH-G4X-YONSEI/LH | MCAT-TH-G4X-LH | GWU | TBD | GWU | TBD |  | Thruster for CANYVAL bus. Note LH and RH orientations are separate, and opposing pin arrangements. Layers are also flipped.
2 | DNI | 1 | THR1:TH2 | MCAT-TH-G4X-YONSEI/RH | MCAT-TH-G4X-RH | GWU | TBD | GWU | TBD |  | Thruster for CANYVAL bus. Note LH and RH orientations are separate, and opposing pin arrangements. Layers are also flipped.
3 | Y | 2 | F1, F7 | SMTRAM2-6-5 | SMTRA-M2-6-5 | Hitech Fasteners, Inc. | SMTRAM2-6-5ET-C |  |  |  | Type SMTRA - ReelFast Surface Mount Right Angle (R'ANGLE) Fastener (Metric)
 | A | Special Note: SPADE TERMINALS not included in BOM (Qty 3) will / may need manual installation

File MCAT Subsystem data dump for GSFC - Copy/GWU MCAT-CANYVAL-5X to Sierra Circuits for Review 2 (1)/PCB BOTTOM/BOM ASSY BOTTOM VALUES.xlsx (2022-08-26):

George Washington University
BOM: | TOP | REV: | 5X
Date | 2015-03-04
Item# | Install? | Qty | Parts | Value | Package/footprint | Distributor | Distributor P/N | Manufacturer | Manufacturer P/N | Device | Description | COPYRIGHT | PCBLABEL
1 | Y | 1 | GBUS-TOP1:H1 | H1-H5-INBOARD-CSK-BUS-CONN | CONN-2X26X0.1-HDR | Samtec | ZW-26-10-G-D-516-090 | SAMTEC | ZW-26-10-G-D-516-090 | H1-H5-INBOARD-CSK-BUS-CONN | H1/H5/Inboard Cubesat Kit Bus Connector |  | H1
2 | Y | 1 | GBUS-TOP1:H2 | H2-H6-OUTBOARD-CSK-BUS-CONN | CONN-2X26X0.1-HDR | Samtec | ZW-26-10-G-D-516-090 | SAMTEC | ZW-26-10-G-D-516-090 | H2-H6-OUTBOARD-CSK-BUS-CONN |  |  | H2
3 | Y | 1 | GBUS-TOP1:G1 | HIROSE-FH40-60S-0.5SV | HIROSE-FH40-60S-0.5SV | Mouser | FH40-60S-0.5SV | HIROSE/HRS | FH40-60S-0.5SV | HIROSE-FH40-60S-0.5SV |  |  | G1
4 | Y | 1 | GBUS-TOP1:G2 | HIROSE-FH40-60S-0.5SV | HIROSE-FH40-60S-0.5SV | Mouser | FH40-60S-0.5SV | HIROSE/HRS | FH40-60S-0.5SV | HIROSE-FH40-60S-0.5SV |  |  | G2
5 | Y | 4 | F4, F5, F6, F7 | SMTRAM2-6-5 | SMTRA-M2-6-5 | Hitech Fasteners, Inc. | SMTRAM2-6-5ET-C | Penn Engineering | SMTRAM2-6-5-DT | SMTRAM2-6-5 | Type SMTRA - ReelFast Surface Mount Right Angle (R'ANGLE) Fastener (Metric)

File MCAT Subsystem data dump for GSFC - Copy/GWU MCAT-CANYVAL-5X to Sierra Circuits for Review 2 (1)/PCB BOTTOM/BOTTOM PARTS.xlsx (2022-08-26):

Part | Value | Device | Package | Description | COPYRIGHT | MF | MPN | PCBLABEL
~~B1~~ | ~~MCAT-4CU-C-PCB/BOTTOM~~ | ~~MCAT-4CU-C-PCB/BOTTOM~~ | ~~MCAT-4CU-C-BOTTOM-V4-BLANK~~ |  | ~~(c) 2015, THE GEORGE WASHINGTON UNIVERSITY~~ |  |  | ~~BOTTOM~~
F4 | SMTRAM2-6-5 | SMTRAM2-6-5 | SMTRA-M2-6-5 | Type SMTRA - ReelFast Surface Mount Right Angle (R'ANGLE) Fastener (Metric) |  | Penn Engineering | SMTRAM2-6-5-DT
F5 | SMTRAM2-6-5 | SMTRAM2-6-5 | SMTRA-M2-6-5 | Type SMTRA - ReelFast Surface Mount Right Angle (R'ANGLE) Fastener (Metric) |  | Penn Engineering | SMTRAM2-6-5-DT
F6 | SMTRAM2-6-5 | SMTRAM2-6-5 | SMTRA-M2-6-5 | Type SMTRA - ReelFast Surface Mount Right Angle (R'ANGLE) Fastener (Metric) |  | Penn Engineering | SMTRAM2-6-5-DT
F7 | SMTRAM2-6-5 | SMTRAM2-6-5 | SMTRA-M2-6-5 | Type SMTRA - ReelFast Surface Mount Right Angle (R'ANGLE) Fastener (Metric) |  | Penn Engineering | SMTRAM2-6-5-DT
GBUS-TOP1:G1 | HIROSE-FH40-60S-0.5SV | HIROSE-FH40-60S-0.5SV | HIROSE-FH40-60S-0.5SV |  |  | HIROSE/HRS | FH40-60S-0.5SV | G1
GBUS-TOP1:G2 | HIROSE-FH40-60S-0.5SV | HIROSE-FH40-60S-0.5SV | HIROSE-FH40-60S-0.5SV |  |  | HIROSE/HRS | FH40-60S-0.5SV | G2
GBUS-TOP1:H1 | H1-H5-INBOARD-CSK-BUS-CONN | H1-H5-INBOARD-CSK-BUS-CONN | CONN-2X26X0.1-HDR | H1/H5/Inboard Cubesat Kit Bus Connector |  | SAMTEC | ZW-26-10-G-D-516-090 | H1
GBUS-TOP1:H2 | H2-H6-OUTBOARD-CSK-BUS-CONN | H2-H6-OUTBOARD-CSK-BUS-CONN | CONN-2X26X0.1-HDR |  |  | SAMTEC | ZW-26-10-G-D-516-090 | H2

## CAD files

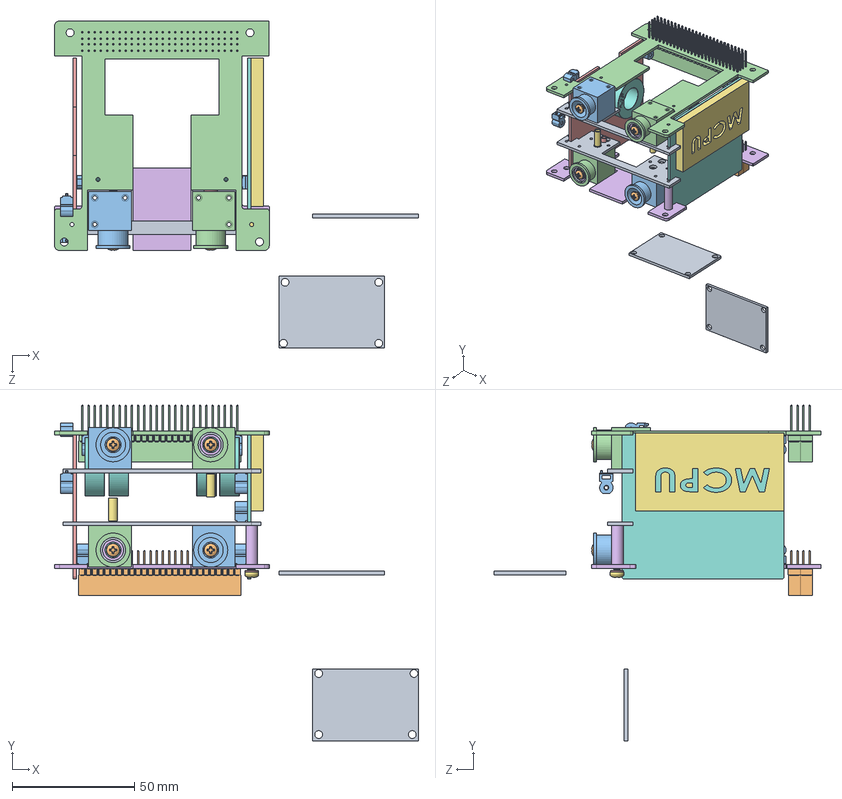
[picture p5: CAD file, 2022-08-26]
MCAT Subsystem data dump for GSFC - Copy/Mechanical/20 DEC - MOD1/TOP_MIDDLE_BOTTOM_STACK.SLDASM
149.1 x 137.5 x 133.9 mm
SPLIT_Middle_TEST x 2
Anode_Screw x 4
Anode_Nut x 4
Holder x 2
Anode_Terminal x 2
Cathode x 2
Cathode_Terminal x 2
Ceramic_Inside x 2
Ceramic_Outside x 2
Spring x 2
Holder_Two x 2
SPLIT_BOTTOM_BOARD_TEST
MCAT-4CU-C-BPR3
SPLIT_TOP_BOARD_TEST
CU
MCAT-4CU-C-BPL3
MCB x 2
Samtec-ESQ-126-38-G-D x 2
SMTRAM2-6-5ET_3D x 9
Samtec-ESQ-126-39-G-D x 2
BELLEVILLE Spring Lock Washer McMaster-Carr 90895A005
r30-5001602
User Library-M3x0_5xL Phillips Panhead Screw
Toroid Core TC229 x 4

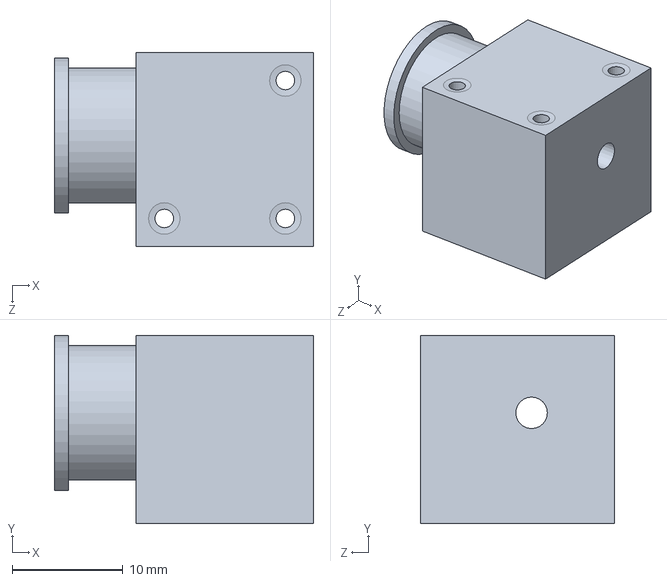
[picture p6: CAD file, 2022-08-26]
MCAT Subsystem data dump for GSFC - Copy/Mechanical/3DEC LUKAS/Holder_Anode_One.SLDASM
23.4 x 17.0 x 17.5 mm

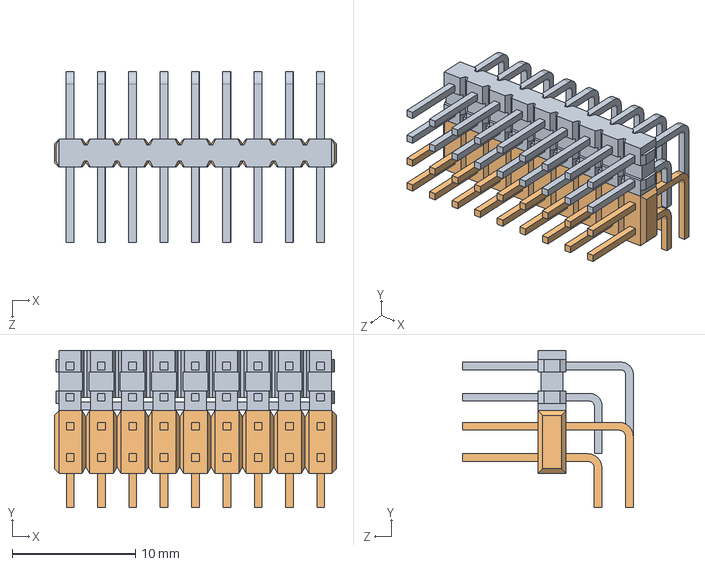
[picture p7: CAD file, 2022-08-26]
MCAT Subsystem data dump for GSFC - Copy/Datasheets/molex/test Assem1.SLDASM
22.9 x 12.8 x 13.9 mm

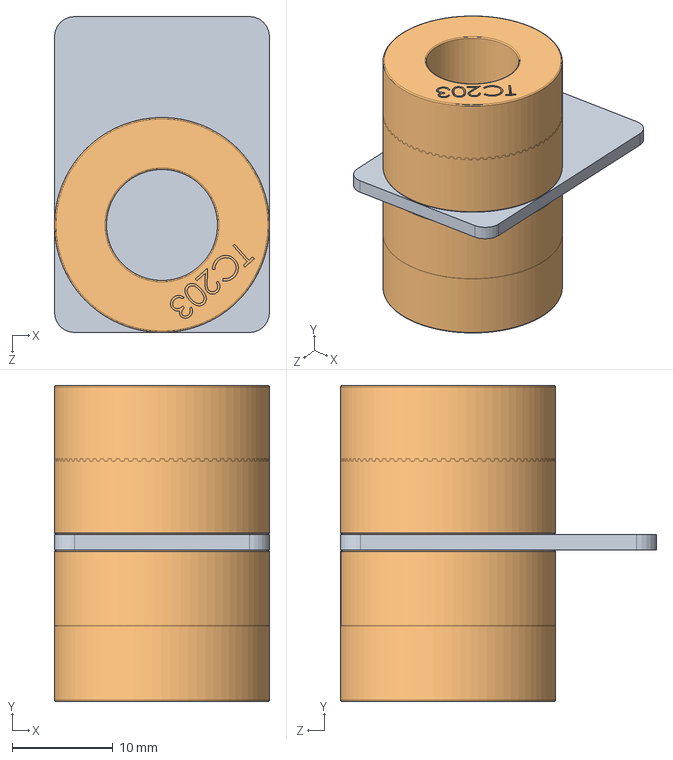
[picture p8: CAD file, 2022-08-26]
MCAT Subsystem data dump for GSFC - Copy/Mechanical/20 DEC - MOD2/MpNL_PPU_IES_STACK.SLDASM
21.3 x 31.3 x 31.3 mm
M1PCB
Toroid Core TC203 x 4

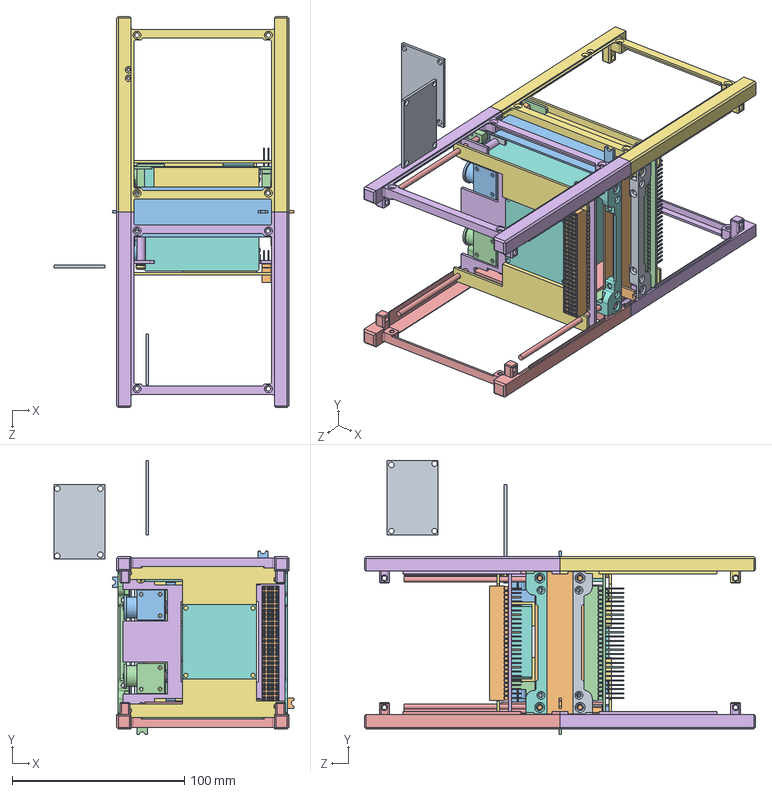
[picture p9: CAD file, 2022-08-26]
MCAT Subsystem data dump for GSFC - Copy/Mechanical/20 DEC - MOD2/MPNL_ISIS_STACK_V2.SLDASM
139.1 x 158.9 x 227.0 mm
MSBR-99
MSBR-112 x 2
MSBR-58
MSBR-70 x 4
MSBR-14
MSBR-41
MSBR-73
MSBR-97
GOMX-INTERSTAGE-B
PRT0001
MSBR-15
MSBR-42
MOUNT_LEFT_NEW
WHEEL_UNIT x 2
SPLIT_Middle_TEST x 2
Anode_Screw x 4
Anode_Nut x 4
Holder x 2
Anode_Terminal x 2
Cathode x 2
Cathode_Terminal x 2
Ceramic_Inside x 2
Ceramic_Outside x 2
Spring x 2
Holder_Two x 2
SPLIT_BOTTOM_BOARD_TEST
MCAT-4CU-C-BPR3
SPLIT_TOP_BOARD_TEST
CU
MCAT-4CU-C-BPL3
MCB x 2
Samtec-ESQ-126-38-G-D x 2
SMTRAM2-6-5ET_3D x 9
Samtec-ESQ-126-39-G-D x 2
BELLEVILLE Spring Lock Washer McMaster-Carr 90895A005
r30-5001602
User Library-M3x0_5xL Phillips Panhead Screw
M1PCB
Toroid Core TC203 x 4

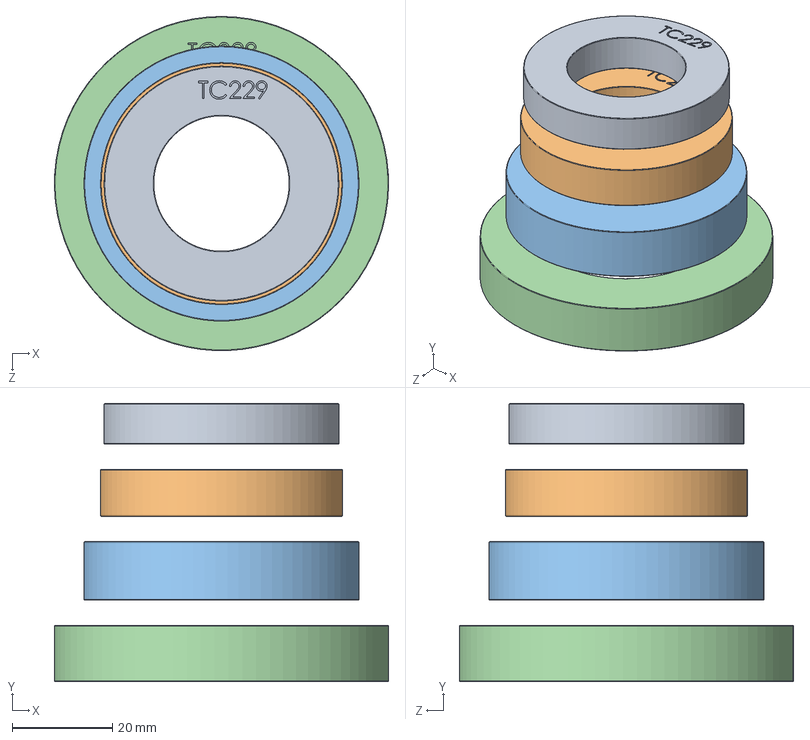
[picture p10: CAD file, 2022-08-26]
MCAT Subsystem data dump for GSFC - Copy/Mechanical/20 DEC - MOD1/Inductor comparison test assy.SLDASM
66.6 x 55.4 x 66.6 mm
Toroid Core TC229
Toroid Core TC236
Toroid Core TC269
Toroid Core TC328

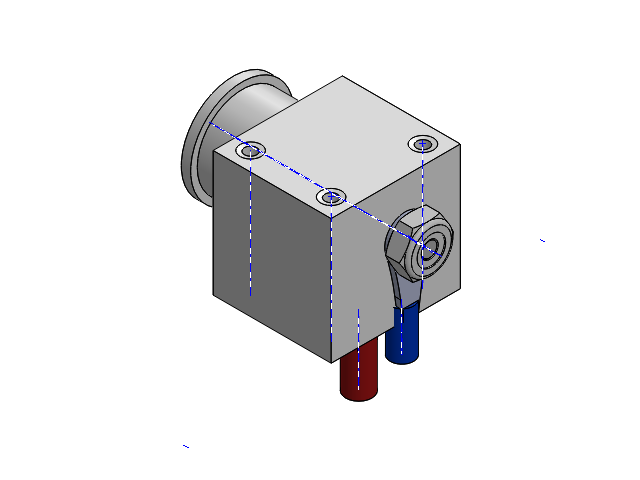
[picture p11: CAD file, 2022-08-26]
MCAT Subsystem data dump for GSFC - Copy/Mechanical/18 JAN - MOD1/Holder_Anode_One.SLDASM
Anode_Screw
Anode_Nut
Holder
Anode_Terminal
Cathode
Cathode_Terminal
Ceramic_Inside
Ceramic_Outside
Spring

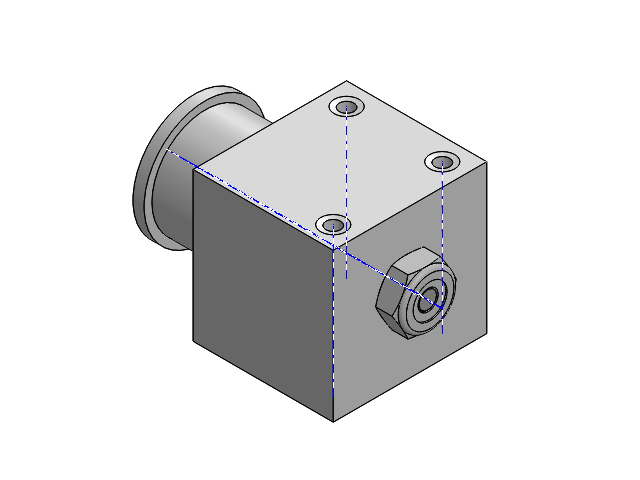
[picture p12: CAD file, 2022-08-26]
MCAT Subsystem data dump for GSFC - Copy/Mechanical/17DEC/Holder_Anode_Two.SLDASM
Anode_Screw
Anode_Nut
Holder_Two

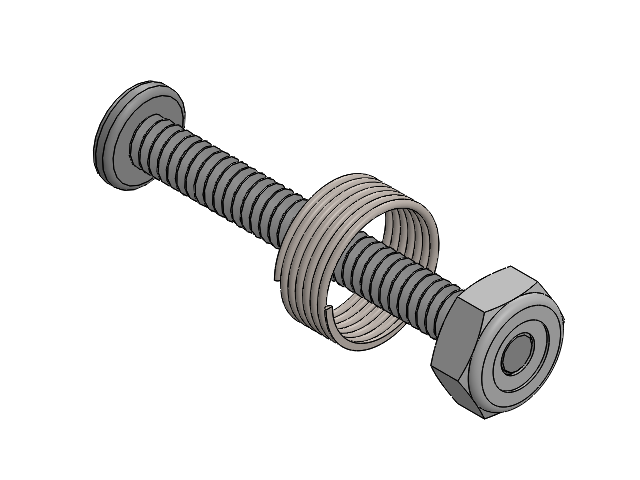
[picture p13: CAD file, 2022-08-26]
MCAT Subsystem data dump for GSFC - Copy/Mechanical/20 DEC - MOD1/Full_Thruster.SLDASM
Anode_Screw
Anode_Nut

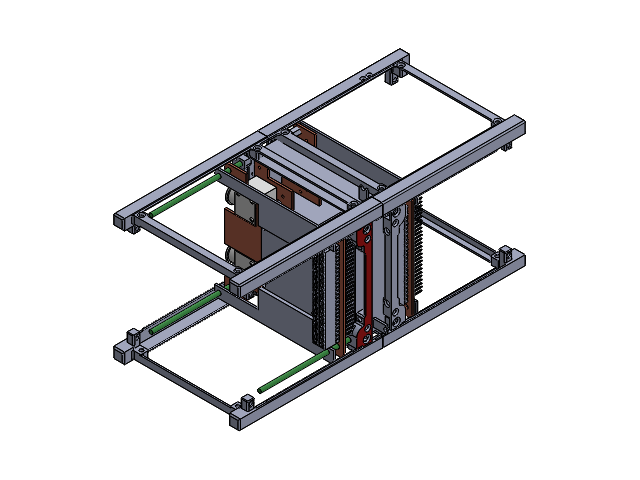
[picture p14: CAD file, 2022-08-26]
MCAT Subsystem data dump for GSFC - Copy/Mechanical/17DEC/ISIS_STACK.SLDASM
MSBR-99
MSBR-112 x 2
PRT0002
MSBR-58
MSBR-70 x 4
MSBR-14
MSBR-41
MSBR-73
MSBR-97
GOMX-INTERSTAGE-B
PRT0001
PRT0003
MSBR-15
MSBR-42
MOUNT_LEFT_NEW
WHEEL_UNIT x 3
Middle_TEST x 2
Anode_Screw x 4
Anode_Nut x 4
Holder x 2
Anode_Terminal x 2
Cathode x 2
Cathode_Terminal x 2
Ceramic_Inside x 2
Ceramic_Outside x 2
Spring x 2
Holder_Two x 2
TOP_BOARD_TEST
Samtec-ESQ-126-39-G-D x 4
Bottom

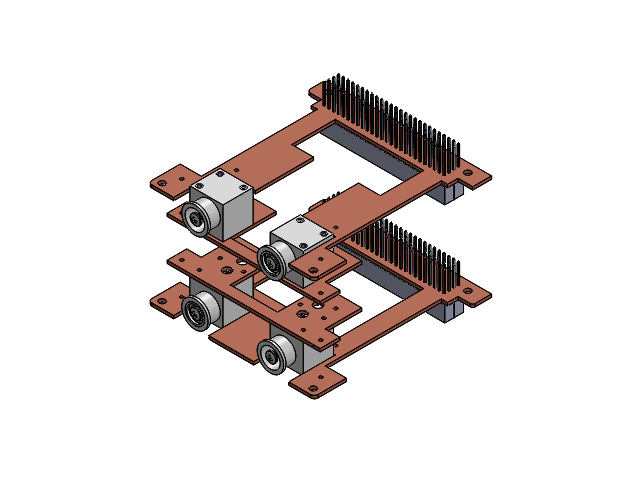
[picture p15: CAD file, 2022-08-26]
MCAT Subsystem data dump for GSFC - Copy/Mechanical/17DEC/TOP_MIDDLE_BOTTOM_STACK.SLDASM
Middle_TEST x 2
Anode_Screw x 4
Anode_Nut x 4
Holder x 2
Anode_Terminal x 2
Cathode x 2
Cathode_Terminal x 2
Ceramic_Inside x 2
Ceramic_Outside x 2
Spring x 2
Holder_Two x 2
TOP_BOARD_TEST
Samtec-ESQ-126-39-G-D x 4
Bottom

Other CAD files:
MCAT Subsystem data dump for GSFC - Copy/Mechanical/26 JAN - MOD1/V7A-BLDC_KAU_ASM_1.sldasm
MCAT Subsystem data dump for GSFC - Copy/Mechanical/17DEC - MOD1/Holder_Anode_One.SLDASM
MCAT Subsystem data dump for GSFC - Copy/Mechanical/17DEC/Holder_Anode_One.SLDASM
MCAT Subsystem data dump for GSFC - Copy/Mechanical/3DEC LUKAS/Holder_Anode_Two.SLDASM
MCAT Subsystem data dump for GSFC - Copy/Mechanical/17DEC - MOD1/Full_Thruster.SLDASM
MCAT Subsystem data dump for GSFC - Copy/Mechanical/17DEC - MOD1/Holder_Anode_Two.SLDASM
MCAT Subsystem data dump for GSFC - Copy/Mechanical/17DEC/Full_Thruster.SLDASM
MCAT Subsystem data dump for GSFC - Copy/CADSOFT Eagle PCB Schematic and Board Editor/BRICSAT-P (2014)/mcat-4cu-b-v1.dxf
MCAT Subsystem data dump for GSFC - Copy/CADSOFT Eagle PCB Schematic and Board Editor/BRICSAT-P (2014)/mcat-4cu-b-v2h%N.DDD.dxf
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

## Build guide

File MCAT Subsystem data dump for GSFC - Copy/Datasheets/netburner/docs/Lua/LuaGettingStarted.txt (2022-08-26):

Introduction
============

This document will explain how to go from a fresh install to building a
project that uses the Lua library, both using NBEclipse and on the
command line. It also contains more general information regarding the
Lua language, idiosyncrasies of the NetBurner implementation of the
interpreter, and references for where to learn more.

The Lua Language
================

To borrow the words directly from the Lua project:

  Lua is a powerful, fast, lightweight, embeddable scripting language.

  Lua combines simple procedural syntax with powerful data description
  constructs based on associative arrays and extensible semantics. Lua
  is dynamically typed, runs by interpreting bytecode for a
  register-based virtual machine, and has automatic memory management
  with incremental garbage collection, making it ideal for
  configuration, scripting, and rapid prototyping.

Lua is a table-based object-oriented language, based around a central
environment table. (The Wikipedia page makes for a good overview)

Language References
===================

Lua Tutorial - http://lua-users.org/wiki/TutorialDirectory

Lua Language Official Site - http://www.lua.org/

Lua 5.1 Reference Manual - http://www.lua.org/manual/5.1/manual.html

NetBurner Implementation
========================

The NetBurner implementation of the Lua interpreter is based on the
official 5.1.4 version of Lua (with some configuration settings coming
from the eLua (Embedded Lua) project ). There are some key things to
note with using the interpreter in an embedded environment:

-   The interpreter does dynamic memory allocation. It does not
    currently have a soft limit (though this is well within the realm of
    reason to add).
-   All numbers are the same data type. The type is set by a compile
    time flag. It is set by default to double
-   Strings are internally cstrings: memory efficient, but resizing,
    concatination, etc. are expensive per usual.
-   Lua does not do arrays in the C/C++ sense. It is possible to use
    tables as arrays in Lua, but they do not store their data in
    contiguous memory like arrays. When used this way, elements can be
    accessed with standard array notation (array[i]). NOTE: Lua array
    notation indexes from 1!

The NetBurner implementation also has a slightly odd method for handling
finding and opening files. As the NetBurner library does not currently
support "mounting" disks and drives at specific file paths, it was
decided to search all potential drives when attempting to open a file.
The order of drive in which Lua searches is configurable via an array in
either the library or the app. The interpreter is, as a consequence,
tightly coupled with the filesystem, requiring the user to configure
predef macros for which filesystems to support and recompiling after
configuring it.

Technical Specifications:

-   Flash usage: ~200k
-   RAM usage: ~200k + 20k per instance of the interpreter

Note: While this is small enough to fit on devices with 512KB of flash,
when combined with the main Netburner libraries, this will consume
roughly 50% of available flash before any additional application code
(C/C++ or Lua) has been added.

Building your first Lua app - NBEclipse
=======================================

After installing the NNDK, you will first want to create a new project
(see the NBEclipse getting started guide for this). We will use this
project as the basis for building one of the example Lua apps. After
creating the project, you will want to import one of the Lua example
applications. These are located in the 'examples/lua/' directory of your
main nburn installation (usually C:\nburn, meaning
C:\nburn\examples\lua\ for the examples directory). If you are prompted
to overwrite "main.cpp", choose "yes".

Next comes configuring the libraries NBEclipse will link to during the
project's build. Go to the project's properties menu (right clicking on
the project in the project explorer and selecting "properties" or
selecting it and hitting alt+enter). Navigate to the C/C++
Build->Settings page of the menu (See picture on next page).

[Adding Libraries]
You should see a page with a tab labeled "Tool Settings" containing a
list with subelements. Select the list subelement "Libraries" under the
element "GNU C/C++ Linker". The right side of the tab will then show a
list of the currently used libraries. At this point, click on the
document icon with a green "+" on it to add a library. At this stage you
will need to add, at the very least, the following libraries (located in
the "lib" directory of your install):

-   lua/Full.a
-   lua/LuaLibs.a, if you imported the ShellApp example (this contains
    the current Lua libraries for interfacing with the main NetBurner
    libraries)
-   FatFile.a and/or StdFile.a, if you would like to use the filesystem

Just hit the "OK" button to save the changes and build the project.

Building your first Lua app - Make
==================================

You can simply copy one of the Lua examples mentioned in the previous
section into a new directory and run 'C:\projectdir> make'. If you would
like to compile in Lua scripts into the application in the same manner
that web resources are compiled in with comphtml, include the following
lines to your makefile:

    CXXSRCS += luadata.cpp
    CREATEDARGS := luadata.cpp
    luadata.cpp: $(wildcard lua/*.lua)
        "$(LUA_DEV)/lua.exe" "$(NBROOT)/pcbin/complua/complua.lua" -i lua -o luadata.cpp

Complua Reference
=================

Full usage information for complua is:

    complua:
        Usage: complua [-h | --usage] [-i <inpath>] [-f <infiles>]
                [-o <outfilename>] [-c <path_to_lua_compiler>] [--rawmode]

        -h or --usage: print this help
        -i: sets the 'include path' where complualooks for lua source files
        -f: comma separated list of source files to process.
                Used in addition to the include path
        -o: sets the path/filename of the output file. Defaults to 'luadata.cpp'

        -c: sets the compiler to use for compiling lua source.
                Defaults to 'C:\Program Files (x86)\Lua\5.1\luac.exe'
        --rawmode: puts complua in rawmode. Rawmode will bypass compiling
                the lua source into bytecode. This will require the parser
                to be included on the device to run the code.

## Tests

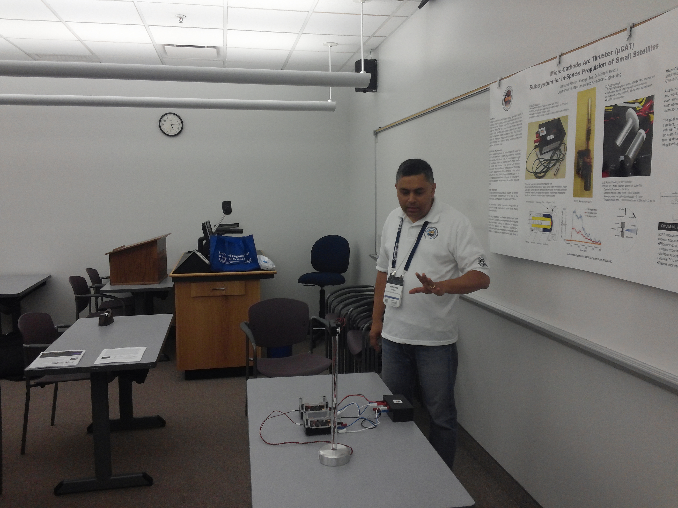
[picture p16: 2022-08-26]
MCAT Subsystem data dump for GSFC - Copy/Images/NASA ARC MCAT PHONESAT EXPERIMENT (2013)/CAM00068.jpg

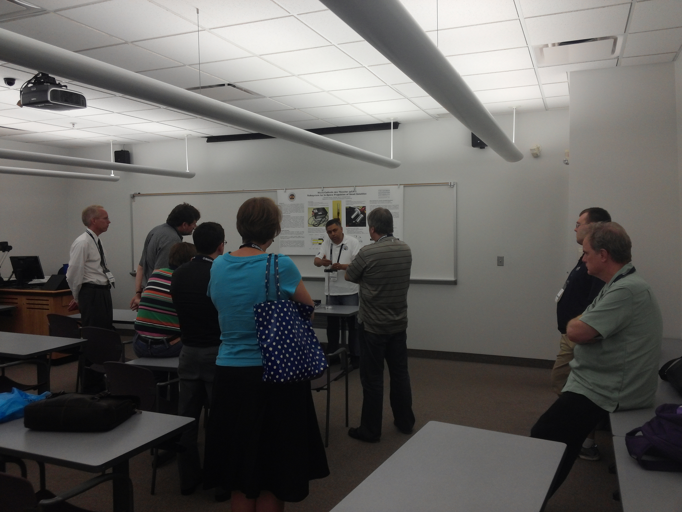
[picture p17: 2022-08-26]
MCAT Subsystem data dump for GSFC - Copy/Images/NASA ARC MCAT PHONESAT EXPERIMENT (2013)/CAM00070.jpg

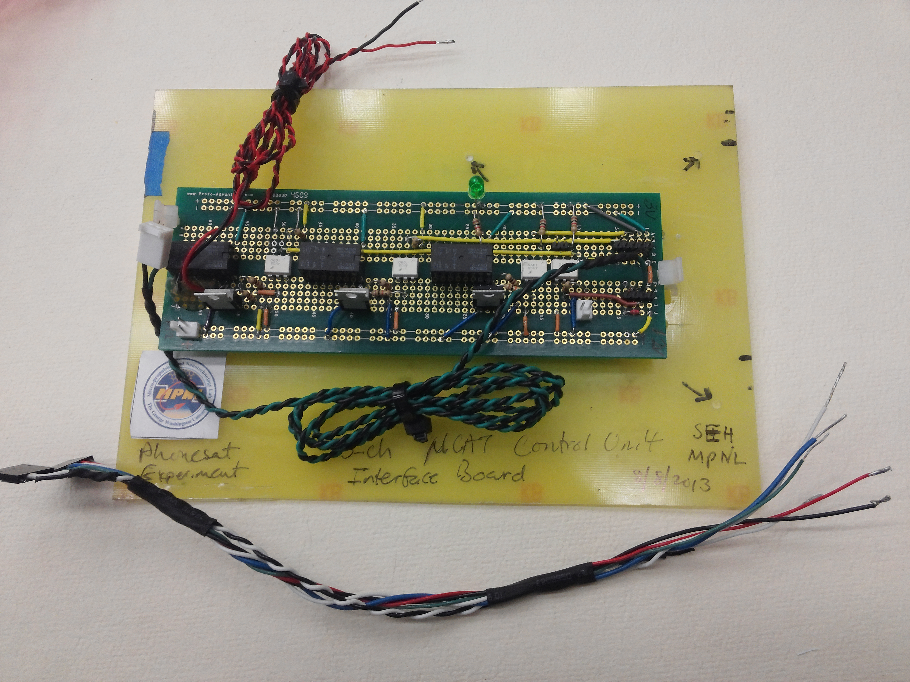
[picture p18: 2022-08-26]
MCAT Subsystem data dump for GSFC - Copy/Images/NASA ARC MCAT PHONESAT EXPERIMENT (2013)/CAM00039.jpg

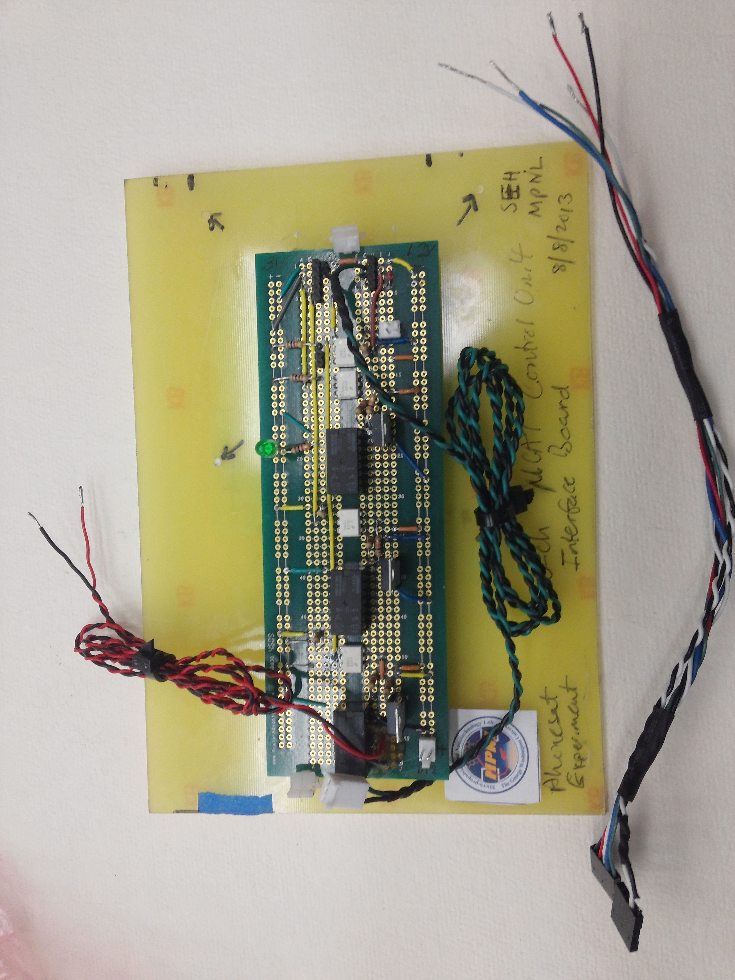
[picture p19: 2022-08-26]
MCAT Subsystem data dump for GSFC - Copy/Images/NASA ARC MCAT PHONESAT EXPERIMENT (2013)/CAM00038.jpg

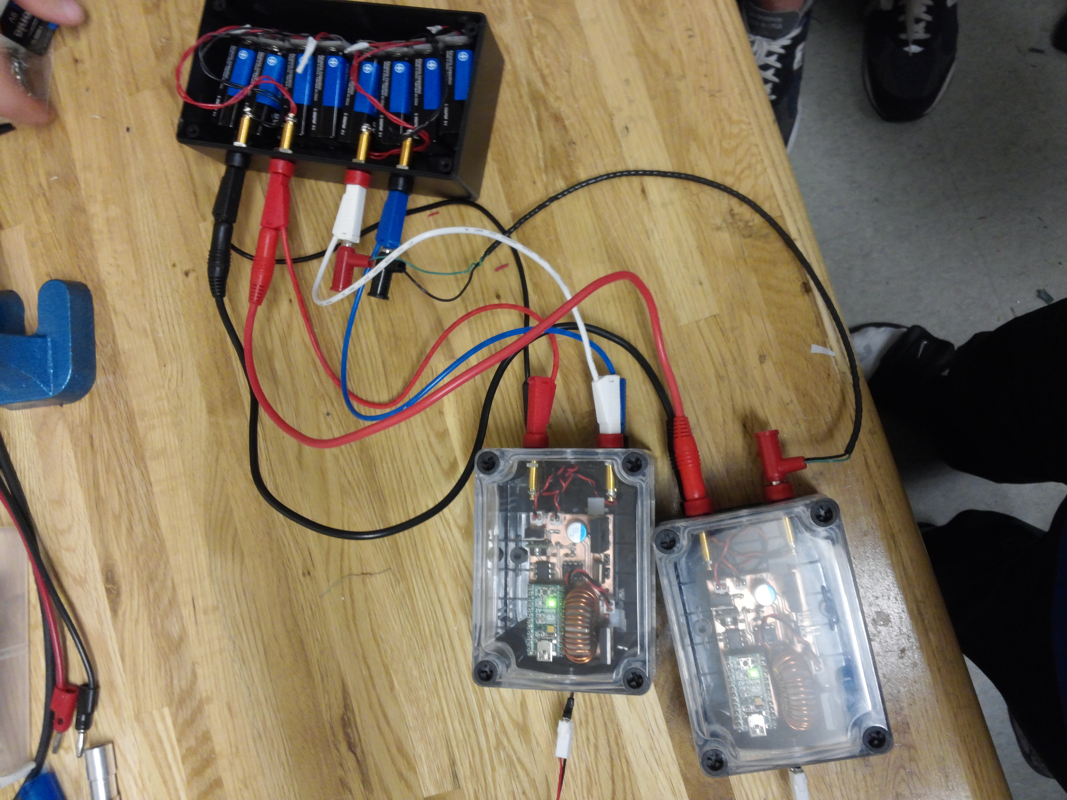
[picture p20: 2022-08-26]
MCAT Subsystem data dump for GSFC - Copy/Images/NASA ARC MCAT PHONESAT EXPERIMENT (2013)/CAM00040.jpg

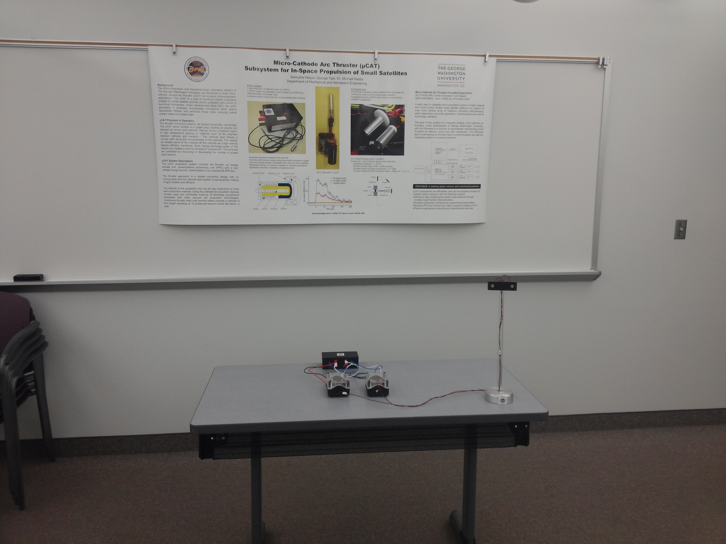
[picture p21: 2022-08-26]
MCAT Subsystem data dump for GSFC - Copy/Images/NASA ARC MCAT PHONESAT EXPERIMENT (2013)/CAM00064.jpg

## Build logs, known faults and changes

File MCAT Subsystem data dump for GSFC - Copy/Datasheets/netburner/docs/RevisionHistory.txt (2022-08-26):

# RELEASE 2.6.4 (November 2013)
## New in this version
* Examples
	* Added PIT timer for the SBL2E
	* Adding wav_player examples to NANO54415 and MOD5441X platforms
* PK70
    * PK70-232CR, -485CR, and -MMSCR devices now supported by secure factory app
* Serial
    * Added SerialSendComplete(), which will check to see if all serial characters are sent
* System
	* Added task time logging feature. To enable it, the system library needs to be compiled with the macro UCOS_TIME defined in constants.h
	* Adding support in uc/os for handling OS_TCBs changing in size without recompiling debug Ethernet drivers. Allows for using stack checking with the debug driver

## Corrections in this version
* MCF5441X
	* Fixed so that chip select mask values for DSPIInit did matches their description and behavior of the qspi driver
	* Fixed multi channel i2c driver to not rely on DEFAULT_I2C_MODULE definition by replacing calls such as i2cinit with multichannel_i2cinit calls internally.
* MOD5441X
	* Fixed pin_irq class error on IRQ6
	* Modified pinio class to reflect hardware revision changes (J1-9/10, J2-17/18)
* SBL2e
	* Documentation updated to more clearly state the 768 stack size value represents 32-bit values, not bytes.
	* Fixed TCP Buffered connect error not clearing error variable
* SNMP
    * Fixed error reporting issues
    * Fixed getNext with null OID
    * Fixed too big error so errors are properly reported and system does not hang
* System
	* WriteHtmlVariable() fixed. Was writing last byte of MAC address incorrectly
	* Fixed problem with incomplete transfers of static web resources
	* Fixed DHCP discover on fast boot with lossy networks
* TCP
    * Fixed scheduling issues with TCP which caused 1 tick busy waits in lower priority tasks
* WIFI
    * Fixed error in AddWifiInterfaceWithName() which could case flash corruption with erratic power

# RELEASE 2.6.3 (July 2013)
## New in this version
* Examples
	* Added Twitter Bootstrap example, a web css framework for UI features on web pages.
	* Added AJAX real time data graph example
	* Added example on SBL2E serial callbacks
* Github
	* Several examples open sourced and moved to github.com/netburner
* HTTP
    * Documented <!-- CPPCALL --> web function. Works like FUNCTIONCALL, but allows support for C++ functions
    * Added robots.txt to disallow search engine crawling of examples by default
* MCF5441X
	* Added DSPI driver and example
	* Added multi channel i2c driver
* NANO54415
	* Added SetDefPinUsage() to set default pin assignments
* SBL2e
	* Added serial callback functions to SBL2e serial drivers
* SSL
	* Added 4096 key support
	* Added RSA_RC4_SHA1 cipher
* System
    * Added FreeBufferList() utility function to free buffer list
    * Added init() and initWithWeb() utility functions. These functions provide standard initialization for apps
* TCP
    * Added NoBlockConnect() non blocking connect function
* Tools
    * MTTTY updated with better USB/Serial port support

## Corrections in this version
* Ethernet
    * Fixed maximum packet size error
* Examples
	* Fixed NTP app/example bug which reduced time accuracy
	* Fixed MCF54415 PWM examples for edge aligned PWMs bug to remove dead time
* MCF5441X
	* Fixed i2c default baud rate
	* IRQ Vector table moved in to SRAM from external DDR
	* Created unified i2cstruct definition, which allows a single type access to all i2c modules
	* Fixed critical processor latency bug which caused 0.5 ms processor hangs
* SNMP
	* Added ability to handle octet writes with embedded zeros
* SSL
    * Fixed TCP socket leak on SSL failures
* System
	* Fixed default timezone parsing so default daylight savings time is 2am, not midnight
* TCP
    * Increased speed of duplicate ack retransmission on a lossy network
* Tools
    * Fixed issue where IPSetup did not see multi interfaces that are not exposed to network

# RELEASE 2.6.2 (April 2013)
## New in this version
* Ethernet
	* Added callback for custom ethernet handlers with RX of ethernet frames
* Examples
	* Examples for StandardStack platforms moved to StandardStack directory hierarchy
	* Added SSH Server example
	* Added BufferedAD example to MCF54415
* NANO54415
	* Added driver for internal RTC
* MOD54415
	* Multiple CAN drivers support added
## Corrections in this version
* MOD54415
	* Fixed ExternalIRQ example
	* Fixed card detection/write protection on off-board memory card reader
* NBEclipse
	* Fixed bug in which Rebuild Libraries failed on imported projects
	* Fixed bug in which MOD5213 failed to load an application on to the device
	* Updated version tag
* Tools
	* IPSetup/Autoupdate run on any socket. This allows multiple instances to run at once
	* IPSetup/Autoupdate bug fix that prevented find from seeing devices with multiple interfaces

# RELEASE 2.6.1 (February 2013)
## New in this version
* Ethernet
	* Added EtherLinkCallBack() callback function to all ethernet drivers. Does not get called in debug mode
	* Moved DoRX ethernet RX function out of individual platforms and made a common NetDoRx function in the system directory. Debug drivers do call this function. Customer modified ethernet drivers should be amended to support this function
* Examples
	* Added DAC example to MCF54415
	* Added OnChip RTC example to MCF54415
	* Added PWM example to MCF54415
	* Added UDPNotify to standard stack examples
	* Added CB34EX support to SecureEthToSer example
	* Added ExternalIRQ example to MCF54415
	* Added EFFS-RAM RAM drive example
	* Added PIT timer example to MCF54415
* L2e
	* Added XON XOFF flow control
	* Added ability to disable serial update on individual ports. Some serial binary data was triggering update logic on the device
* MCF5213
	* Added XON XOFF flow control
	* Added ability to disable serial update on individual ports. Some serial binary data was triggering update logic on the device
* MCF54415
	* Added proper support to sim structure for RTC and DMA
	* Added pin_irq class support
	* Added beta DMA SPI driver
	* Added DSPI driver and examples to demonstrate usage
* LUA
	* Added support for LUA scripting language
	* Added several examples to demonstrate LUA usage
* System
	* Added getFunctions to pinIO. This allows current pin function to be read
	* Smarttrap now includes additional message which reports spurious interrupts
* Tools
	* Added no reboot option to autoupdate
	* Added BatchUpdate script in pctools. This script can be used to batch update several NetBurner modules with a single application
	* NBEclipse updated for OSX and Windows
	* NBEclipse now support names in NBLIBRARY files. This file allow NBEclipse to automatically link libraries in all projects.
## Corrections in this version
* AutoIP
	* Changed getState member function from private to public. This function returns the current state of the auto IP client
	* Fixed issue where disabling AutoIP in predef.h was causing compilation errors.
* DHCP
	* DHCP is now more random in initial DHCP request. This helps prevent IP conflicts when multiple devices come online simultaneously
* EFFS
	* Fixed mutex bug that generated problems when simultaneous SD cards are used on MOD5441X
	* Changed ram_mcf.cpp from a per-Platform file to a per-Project file. This allows for different sized drives.
* HTTP
	* Fixed extraneous 0xFF sent at the end of some http responses
* I2C
	* Added mutex guards to i2cmulti and i2cmaster headers. Including both now results in a compile error
* MCF54415
	* Fixed missing sim error
	* Fixed support for both can devices
* NANO544115
	* Fixed spaceleft() function, which calculates head size
	* Fixed startup flash memory sequence error
* SBL2e
	* Factory application properly enabled RTS when flow control is disabled
* System
	* putled() and getdipsw() functions now have proper support for platforms that don't use these functions
	* Added microsecond delays to HiResTimer
	* Fixed incorrect constant in MOD5270 pinconstant.h
* WIFI
	* RTL8711 library support was mistakenly removed from 2.6.0. This has be re-added

# RELEASE 2.6.0 (September 2012)
## New in this version
* Examples
	* Added EFFS/WIFI shared QSPI example
	* Added external RTC clock example to MOD54415
* Tools
	* CompHTML now allos user to ignore individual files
## Corrections in this version
* Installer
	* Fixed case where USB driver not installed automatically
* MOD54415
	* Fixed unchangeable timetick bug
	* Added missing can driver
* NANO54415
	* Fixed unchangeable timetick bug
	* Added missing can driver
* SBL2e
	* Fixed TCP duplicate ACK bug
* Tools
	* Added required dll to MTTTY

# RELEASE 2.6.0.026 BETA ADDENDUM (AUGUST 2012)
## Corrections in this version
* I2C
	* Fixed build error in mod5213
* MOD54415
	* Fixed usable memory space. Was 16MB, now up to 32MB available
* NANO54415
	* Added new pit timer access class
* System
	* Fixed system library build error

# RELEASE 2.6.0.024 BETA ADDENDUM (AUGUST 2012)
## New in this version
* Examples
	* Merged multiplatform SSH examples in to one app
* MOD54415
	* Added RapidGPIO example (Pulses GPIO pin at max speed)
* NANO54415
	* Added PDF documentation
* SBL2e
	* Added new Software Watchdog example
* Utility
	* Fixed slow bootup time caused by AutoIP
	* Added documentation for AutoIP functions to NetBurner Runtime Librarys PDF

## Corrections in this version
* EFFS
	* Fixed race condition which caused unreadable drive error
* MOD54415
	* Fixed I2C driver bug
* NBEclipse
	* Fixed debugging timeout/disconnect/breakpoint errors
	* Fixed missing library error when changing platforms in a project
* PK70 NTP Application
	* Fixed username/password bug
	* Fixed floating point precision bug
* TCP
	* Fixed multihome error state when using the connect() function.

# RELEASE 2.6.0 BETA ADDENDUM (JUNE 2012)
## New in this version
* MOD5441X
	* Added I2C driver
	* Added RTC driver
* NANO54415
	* Added I2C driver
	* Added interrupt definitions
* Utility
	* Added AutoIP capability and example on use

## Corrections in this version
* Installer
	* Fixed compcode hang bug introduced in previous beta
	* Fixed missing platform documents in new installs
* MOD5441X
	* Added missing InitNetworkGDB_and_Wait() function
* NANO54415
	* Fixed SPI flash section misalignment bug
	* Fixed time ticks setup. Was running to quickly and ignored the settings
* NBEclipse
	* Fixed missing m68k-elf-gdb target in new run configurations

# RELEASE 2.6.0 BETA (MAY 2012)
## New in this version
* New products
    * NANO54415
    * MOD5441X
* FAT
    * Added the ability to support multiple drives/SD Cards
* IP
    * Asymmetric route checking added
* OS X
    * Support added for Mac
* PC Tools
    * CompHTML now supports arbitrary file types and extensions. To add/modify a file type, modify pcbin\MIME_Magic.txt
    * TCP Send - Allows you to send a file from PC to module over TCP
    * Compcode - added binary output option
* RTOS/UCOS
    * Moved UC/OS initialization to allow global static objects to use rtos functions
* Utility
    * Added HiResTimer. An easy to use configurable time delay/stopwatch functionality with a DMA timer

## Corrections in this version

* DHCP
    * Fixed bug in which DHCP was not handling infinite rebind times
* Ethernet
    * Improved Ethernet status reporting in dynamically changing speed and duplex configurations
* FTP/TCP
    * Fixed 32Kb long get request attack which caused NetBurner web server to lock up.
    * Fixed FTP server bug in which directories were not properly displayed by some clients
* I²C
    * Cleaned up I²C bug that caused a periodical lock up during a re-init call.
    * Fixed timeout bug in MultiI2CRestart()
* IP
    * Fixed IP Checksum error in some debug releases
    * Fixed broadcast filter for fragments and for broadcast packets not on the local subnet.
* L2E
    * Fixed bug in which buffered tcp data object had an error in report charavail().
    * Fixed bug with receiving zero window probe requests
* SSL Certs
    * Fixed error in conversion code that incorrectly converted some certs
* SSL Sendmail
    * Fixed bug in which TCP socket was lost left half open on an SMTP email failure
* UC/OS
    * Fixed race condition during boot up with slow-boot memories (SERIAL). Does not affect existing platforms, might affect custom platforms

Release 2.5.3 (Jan 2012)
 New in this version
	* New Platform
		o MOD54415 support added
		o PINK example added
	* EFFS
		o Upgraded EFFS-STD from 1.631 to 1.91.
			: With version change, you must reformat file systems using older versions. This does not apply to SD cards using the EFFS
		o Added multi-threading support
		o Wildcard searches now follow DOS conventions ( *.* for files, * for everything )
	* HTTP
		o Added 2 new globals for HTTP server
			#define MAX_HTTP_PENDING_SOCKETS (5) // Number of sockets allowed to be pending on listening socket, performance will degrade < 3
			#define MAX_HTTP_CONNECTED_SOCKETS (3) // Number of sockets allowed to be connected to http server simultaneously
	* I2C
		o Added slave i2c callback functions
	* Mail
		o Added port parameter option to SendMailAuth
	* PC Tools
		o Added java version of autoupdate and ipsetup for upcoming OSX release
		o Added command line interface to ipsetup. Allows for script support
	* System
		o Added dual boot and ABOOT commands

 Corrections in this version
	* Ethernet
		o Fixed IP source address error in Ping and SendICMPError. These functions could generate corrupt 	packets when programmed incorrectly.
		o Debug ethernet driver functions pulled out to allow changing of system constants in the debug ethernet driver
		o Fixed rare soft reboot lockup on MOD5272 micrel PHY
		o Fixed problem with MOD5272 failing to communicate with PHY after soft reboot
		o Fixed some newtork code flow to remove confusing conditionals
		o Modified checking of PHY ID to focus on OUI ID so most Micrel, Davicom, National and AMD PHYs should now work without any software modification.
	* HTTP
		o Fixed IE9 issue in which IE9 opens 2 sockets for every web page and handles all communication on the second socket, leaving the first socket hanging. All open sockets are now placed in a select statement to handle this situation properly
	* L2e Platform
		o Fixed sprintf error case
		o Fixed PostHandler bug that occurs when searching through multiple filenames
		o Fixed Get handler to not capatilize all url encodiing
		o Fixed bad timeout in connect
		o Fixed bad pointer on failed connect
	* MCF5272
		o Fixed Flash size error in monitor ld file
		o Fixed UDP error in which network driver would sometimes deliver out of order or duplicate packets when receiving full size ethernet frames
	* PC Tools
		o Improved network communication on Win7/Vista
		o Fixed clinetool for script support of autoupdate
		o Fixed pythonfind example to work with 3.0 release of Python
		o Fixed socket open error in TCPUpdate
		o Fixed javascript MIME encoding in comphtml
	* RTOS
		o Fixed trap occuring when UCOS_TASKLIST was enabled
		o Increased performance for applications using atomicity macros
	* Serial
		o Fixed SendBreak() function for use with RS-422/485 mode
		o Added custom baud rate support for MCF5272 processors
	* SNMP
		o Fixed case when SNMP task is stuck in a loop when a string larger than 254 chars is written.
	* SSH/SSL
		o Fixed memory leak/cleanup support in TCP error state
	* System
		o Fixed itoa library function for large hex values
		o Fixed printf bug, not printing all characters of an unsigned long decimal (5213/L2e Devices)
	* TCP
		o TCP errors in Release 2.5.2 are significant and can the TCP stack and/or user tasks to permanently hang up..
			Symptoms include:
			o Locking TCP connections
			o Freezing web pages after consecutive reloads
			o Freezing web pages after days of idle time.
		o Fixed TCP timeout processing of closed sockets
		o Fixed TCP hangup and half closed sockets memory leak
		o Performace imporvement
		o Fixed incorrect arp caching scenario
		o Fixed Accept close race in TCP
		o Fixed bug that can cause TCP task to remain in infinite loop.

Release 2.5.2 (Jan 2011)
 New in this version
	* L2e family
		o Added I2C driver
		o Added I2C example
		o Added NTP example
		o Added advanced SBL2e examples (SendmailCallback, TcpClientCallback, TcpServerCallback, TcpWriteCallback)
	* PC Tools
		o Added NTPTest application
	* PK70
		o Added FPGA blade board documentation and example

 Corrections in this version
 	* L2e family
		o Fixed bug in serial rx state machine
		o Fixed tcp_printf error
		o Added stack check ability to taskscan
		o Fixed error in large integer printf
	* SB70
		o Fixed a makefile error during SB70B builds
	* TFTP
		o Fixed intermitent TFTP on noisy networks

Release 2.5.1 (Dec 2010)
 New in this version
	* New Platform
		o Released NTP Blade board
	* FTP
		o Added ftpd timeout ability
	* HTTP
		o Added function to allow http page remap
	* L2e
		o New GPIO level shifting example
		o Enhanced support using 2 serial ports in dual serial factory app
	* System
		o New malloc/mallinfo example

 Corrections in this version
	* FTP
		o Fixed buffer overrun when renaming files during an FTP session
	* L2e
		o Fixed SBL2e autoupdate bug that corrupted platform name during update
		o Added dynamic DNS to L2e factory app
		o Updated factory app UI
	* SB70LC
		o Fixed DNS cache clear on connect bug in factory app
	* SB700EX
		o Fixed DNS cache clear on connect bug in factory app
		o Fixed RTC failure during some initialization scenarios
	* System
		o Increased speed and reliability when updating application of Ethernet
		o Fixed GetReleaseTag() usage error
	* Tools
		o Increased default font size in MTTTY

Release 2.5.0 (Sept 2010)
 New in this version
	* New Platform
		o Added support for SBL2eX
		o Added support for SBL2eXA
		o Added support for SBL2e Chips
	* SSL
		o New new mail example
		o New mailto function
	* SSH
		o Added SSHServerUserKey and SSHMinimalServer examples
	* PPP
		o Added 3rd UART support
		o Added magic number support
	* WIFI
		o Added QOS support
		o Improved ad hoc support
		o Added regulatory domain support
	* L2e
		o Added new pins class
		o New NTP Client code and example
		o New http password example
		o New post example
	* System
		o Added ATCommands
		o Added const char * GetReleaseTag(), which returns the current NNDKRelease tag
		o Added OSSimpleTaskCreateSRAM, OSSimpleTaskCreatewNameSRAM to create tasks in SRAM
	* TCP/UDP
		o Added selective acknowledgment (SACK)
		o Added window scaling options
		o Added out of order TCP user options
		o New functions TcpGetSocketState, TcpAllDataACked, WaitForSocketFlush (see tcp.h)

 Corrections in this version
	* SSL
		o Fixed buffer error related to simultaneous RX/TX
	* Tools
		o Fixed crashing bug in comphtml
		o Updated Virtual Comm application with bug fix and added documentation
	* MOD5213
		o Fixed bad system header in iosys.h
	* MOD5234
		o changed interrupt levels and priorities in TPU to avoid conflicts
	* MCF5208 (License)
		o Fixed interrupt vector issues with SetIntC
	* L2e
		o Fixed monitor to set proper 50MHz CPU frequency
		o Fixed serial timeout problem in L2e factory applications
		o Fixed Post HTML bug in which variable would lose their last char
		o Fixed bug that sent extraneous RST packets
		o Fixed bug that caused lost SYN packets on connection, slowing down TCP connections
	* System
		o GATHER_RANDOM is now enabled by default
		o Fixed MS Vista/7 issue that caused autoupdate and IPSetup to sometimes fail
		o Updated timezones calculation feature
		o Updated taskscan stack size reporting to show bytes instead of DWORDs
		o Fixed buffer overrun error in mailto
		o Fixed error in mail subject lines
		o Fixed stack alignment in OSTaskCreate when passed misaligned stack
	* TCP/UDP
		o Fixed TCP timeout race condition
		o Fixed TCP close race condition
		o Updated window size on TCP connect and accept to not be 0
		o Fixed ARP race condition causing network buffer corruption
	* I2C
		o Changed interrupt from level 5 prio 1 to level 3 prio 4 to avoid CAN conflicts

Release24_RC2 (December 10, 2009)
 New in this version
    * MAIL
        o Added date/time stamps to outgoing email messages
    * EFFS
		o Support for Compact Flash cards up to 128GB
	* TCP
		o Added extra parameter to Connect() function allowing specification of interface

 Corrections in this version
    * FTP
		o Increased FTP Buffers to support up to 256 byte paths and filenames
		o Fixed flow control issue with f_read/f_write in FTP example applications
    * EFFS
		o Fixed size reporting with large SD cards

    * Debug
		o Fixed debug warm reboot bug with Micrel PHY

Release24_RC1 BETA (November 3, 2009)
 New in this version
    * SBL2e
          o Added support for new platform
    * SB700EX
          o Added support for new platform
    * WIFI IEEE802.11b/g Network Interface Controller (NIC)
          o WIFIUG-200CR (RealTek RTL8711 Wireless LAN NIC) released.
          o Added WIFIUG_200CR driver and support (rtl8711Library)
          o Added progress routine callback to support managing connection changes.
    * CAN
          o Added method to send RTR (CanSendRTR).
    * uC/OS
          o Added post to front of queue & example (OSQPostFirst). See uC/OS RTOS Library manual.
    * STDIO
          o Added function: int CurrentStdioFD( int stdio_fd ) to return current FD mapped to stdio
    * NETBIOS
          o Added NETBIOS naming and example program.
    * TCP
          o Added keep-alive functionality and example.

 Updates in this version
    * WIFI Interface
          o Removed WIFI_100CR driver (Netgear MA 701, Intersil PRISM) available through support.
          o Removed NXP BGW211g driver.
          o Added parameters to WIFI interfaces to support future devices.
    * Examples
          o CB34EX-SerialToEthernet - Added LED feedback.
          o TestDHCP - Added state debugging messages.
          o multicast - Improved feedback messages.
          o EFFS STD - new example for standard flash file system.
          o UDP - Added Simple UDP to Serial example.
    * Mail
          o Added SSL mail support & example (Requires Embedded SSL & SSH Security Suite license)
    * SSL
          o Increased key size to 4096. Large key size affects performance.
          o Client authentication.
    * Tools
          o Silent installation of USB driver for MOD-DEV-100(70), driver is digitally signed.
    * Real Time Clock
          o Applies to hardware platforms that support a real-time clock. Added alarm and timer functions.
            Both of these functions use external IRQ 1.

 Corrections in this version
    * ARP
          o Fixed possible race condition in which an ARP entry could be aged out while being used.
    * DHCP
          o Fixed problem with rebind, in which it was possible a DHCP rebind request would not request
            the previously assigned IP.
    * HTTP
          o Corrected buffer overrun on post of large web pages.
          o Fixed problem in which HTTP POSTs or GETs would fail if the data was received in more than
            one packet.
    * Ethernet
          o Corrected PHY latching on soft reset on Modules with MICREL PHY.
    * SSL
          o Corrected multiple socket connection data contention.
    * Serial
          o Corrected hardware (RTS/CTS) and software (XON/XOF) flow control issues.
          o Merged serial software driver source code for similar platforms.
    * Tools
          o Corrected printf floating point reentrancy data contention.
    * MAIL
          o SMTP: Corrected error condition in which SendMail() and SendMailEx() would not immediately release the
            TCP socket if the connection was refused by the SMTP Server.
          o POP3: Modified function POP3_RetrieveMessage to return error if message is bigger than the given buffer
            size instead of stalling.
    * PPP
          o Modified PPP LCP NAK and modem initialization to prevent deadlock conditions during multiple attempts
            to connect. Fixed changing of ACCM before and after LCP negotiation and after LCP negotiation.
    * I2C
          o Improved reliability of receving bytes in I2C driver.

Release23_RC7a (April 30, 2009)
 Updates in this version
    * Addendum to RC7
          o Fixed MOD5213 compilation issue
          o Fixed NBEclipse debugger optimization error

Release23_RC7
 Updates in this version
    * EFFS
          o Added option to enable CRC checking on SD/MMC cards
          o Fixed EFFS retransmission issue affecting connections with slow speed
          o Fixed EFFS date formatting bug
    * Examples
          o Added NTP timezone examples
          o Added TCP Keep Alive example
    * I/O
          o Added speed enhancements to A/D driver on PK70 multi blade NBPKBM-100CR.
          o Adjusted CAN timing for the 1mbit baud to be 983KHz instead of 1.02mhz.
    * Network
          o Added tcp keep alive
          o Added more random tcp sequencing to prevent sequence guessing attacks.
          o Added ability to transmit using UDP fragments. Must turn UDP fragment option on in predef.h to send or recrive UDP fragments
          o Added Etherlink() function to debug Ethernet driver.
          o Fixed bug in which the debug version of the Ethernet driver did not respong to ARP requests properly.
          o Add DHCP option 60 (Vendor Class-Identifier) which should cause DHCP Server to send option #43 (vendor specific) in DHCP reply
    * NNDK Kit and Build System
          o Added support for SB70LC platform
          o Added support for SB700EX platform
          o Added support for PK70 blades: Quad 232, Quad 485
          o Added USB PC serial driver to release for dev boards with a USB interface
          o Added CPU type definitions for common files
          o Fixed bug in PK70 digital I/O on multi blade NBPKBM-100CR
          o Fixed IOBoardRTC.h functions so they are redefined into rtc.h
          o RTC clock chip was discontinued by vendor. Added new RTC drivers to support RTC chip replacement on development boards.
          o Added three new function: RTCSetAlarm(bts), RTCTimerSeconds(count), (RTCTimerMinutes(count). These functions can be used to set an external timer or alarm to interrupt and/or wake up the modchip from low power mode. The interupt is set on IRQ1, and the interrupt level is 1.
    * Security
          o Added SSH support and examples as part of optoinal SSL sofware package
          o Added SSL Client Certificate support and example
          o Fixed SSL Client buffer leak that could occur for multiple simultaneous client socket connections
          o Increased ssl maximum key size to 4096 bits. Using keys this large will significantly increase negoation times by a factor of 32.
    * Serial
          o Fixed RS-485 half-duplex to work on all h/w serial ports.
    * UCOS
          o Fixed UserMain task stack size bug.
          o Fixed printf multi-threaded re-entrency bug
    * Web
          o Fixed XML bug where dynamic pages' lengths could not be determined beforehand.

Release23_RC1
 New Features
    * Upgraded to Eclipse 3.4 Ganymede Release
    * IP/Platform information stored
    * Auto-created run configuration (One-Click Build and Load)
    * Platform Properties file format supported for quick addition of custom platforms
    * NBEclipse can now be run as an independent plug-in to a standard Eclipse install
    * GNU Code formatter now included (Right-Click->Source->Format)
    * Can now directly connect to debug session without updating new code
    * Rebuild System files revamped and sped up

Release22_RC3
 Features
    * DHCP renew fix

Release22_RC2
 New Features
    * Added Fast RAM feature. This feature uses on-chip fast static ram for RTOS stacks, variables and network buffers. This should improve task switching, interrupt latency and network performance. In most applications it will improve performance by 50%. This feature is on by default. If you are using on-chip SRAM for your own purposes, you will need to disable this feature in \nburn\include\constants.h.
    * Added support for Email MIME attachments as text or binary, and associated examples.
    * Added a build status report each time NBEclipse builds a project that shows flash usage, ram usage and the tools revision number.
    * Added ability to name uC/OS tasks, and names are now supported by Task Scan, Smart Traps and the NBEclipse debugger. The new function are:
          o BYTE OSTaskCreatewName( void ( *task ) ( void *dptr ),
          o void *data,
          o void *pstktop,
          o void *pstkbot,
          o BYTE prio, const char * name);
          o OSSimpleTaskCreatewName( void( *task ) (void *dprt ),
          o BYTE priority,
          o const char *name )
 Example Programs
    * Reorganized the c:\nburn\examples directory to group examples by function, such
    as TCP, Serial, FTP, etc.
    * Changed web page image in PK70 factory example from mod-dev-100 to PK70.
    * Added FlashDemo example to \nburn\examples\Mod5270, Mod5234 and Mod5282.
    * Added Email attachment examples in \nburn\examples\Email .
    * Added RTOS examples from Programmers Guide to \nburn\examples\RTOS.
    * Added ChangeIP example from Programmers Guide to \nburn\examples.
    * Added DNS Device Name example.
    * Added DNS example.
    * Added TCP examples for clients, multiple sockets and use of the select() function to \nburn\examples\TCP.
    * All web page related examples moved to \nburn\examples\web. Embedded Flash File System
    * Added command parser options to the example EFFS_HTTP to allow SD card formatting and usage reports using MTTTY and the serial port.
 Documentation
    * Updated the MCF5272 Freescale Reference Manual to the latest revision.
    * Added Sendmail attachment function calls.
    * Added schematic for revision 1.09 mod-dev-100 development board. Hardware
    * Support for the MOD-DEV-70 development board with the MOD5234 has been added. "ioboard.c" is removed and replaced with "ioboard.cpp", with changes made to the "makefile" to take this into account. This change in file extension is required in order to include support for C++-specific syntax used by the ETPU system files, and the if-else condition abbreviation statements.
    * Support for the MOD-DEV-70 development board with the MOD5282 has been added. "ioboard.c" is removed and replaced with "ioboard.cpp", with changes made to the "makefile" to take this into account. This change in file extension is required in order to include support for C++-specific syntax used by the if-else condition abbreviation statements.
    * Follow-up on MOD5234/82 compatibility with MOD-DEV-70 development board: Comments have been added near the top of each platform's ioboard.cpp file to indicate what pins are being used for getdipsw() and putleds(), and the cautions of using the pins for a custom application while calling the two functions mentioned.
    * Added support for new NXP Real Time Clock used on mod-dev-70 and mod-dev-100 new revision development boards. The previous RTC has been discontinued by the manufacturer.
 Software
    * FTP Client and Server Compatibility Change. The definition of FTP_OK and FTP_FAIL were different for the FTP Client and FTP Server. All references to FTP_OK and FTP_FAIL used in FTP Server functions (denoted by FTPD in function names and file names) have been changed to FTPD_OK and FTPD_FAIL in the following files: \nburn\include\ftpd.h, \nburn\system\ftpd.cpp and \nburn\examples\effs\effs-http\fat_f.cpp. If you have an application based on the EFFS-HTTP or EFFS-FTP example code that uses ftp_f.cpp, you will need to replace FTP_OK and FTP_FAIL with FTPD_OK and FTPD_FAIL.
    * The GatherRandom function used by SSL had a bug in that corruption could occur for multiple interrupts. This has been corrected.
    * The TCP SockReadWithTimeout( ) function had an error where it could get stuck in an infinite loop when TCP was stressed with a half-open denial-of-service attack. This has been corrected.
    * Fixed stream update functions used by EFFS update, HTTP update and TCP update for PK70 platform.
    * Added gratuitous ARP function.
    * Fixed DHCP Renew to include the device name with the renew request.
    * Removed leading whitespace in FTP server functions that list file names. This had prevented some FTP Clients from properly displaying the file names.
    * Fixed a bug in passive mode FTP that could prevent some connections through firewalls.
    * Fixed problem with writesafestring() and writeallsafestring() functions in which the last character was not written.
    * Fixed problem with the HTTP password function in that caused erratic behavior when HTTP reserved characters were used.
    * Added return error code when OSTaskCreate( ) is called and no more task control blocks are available.
    * Added extern function prototype declaration for GetPreciseTime(). With this function call, one can use a higher resolution time tick than the default "TimeTick" on the MOD5234, MOD5270, and MOD5282. Resolutions are ~0x.868 microseconds per tick for the MOD5234 and MOD5270, and ~1.929 microseconds per tick for the MOD5282.
    * Upgraded EFFS to version 3.3.1, which adds SDHC support for SD cards larger than 2GB.
    * Fixed I2C to recover when address is not acknowledged with the SendBuf and ReadBuf functions. BasePutChar() has been modified to test whether the member function WriteData() wrote a character to the buffer successfully or not. In the event that WriteData() was not successful, SetDataAvail() would be called anyways to indicate that the file descriptor has available data in the pool buffer for reading, when it really does not. This would cause the select() function in serreadwto() to indicate there is data available, while the member function ReadData() will always return '0', causing an endless while loop.
    * Modified SerialClose( ) to reset the buffer FIFO instead of calling init to correct a possible memory leak.
    * Fixed outgoing ARP problems when running the debug Ethernet driver. This would affect debug builds in which the NetBurner device was making an outgoing connection to a computer other than the on used for debug.
    * Added drivers and examples for new PK70 blade boards.

Release21_RC2
 NBEclipse
  Now supports Vista
  Updated CDT core to 3.1.2
  Updated GCC compiler to 4.2
  Updated Eclipse core to 3.2
  Corrected problem in which the project properties advanced tab were not saved
  Corrected problem with memory map range in MOD5234 and CB34EX
  Added platform support for PK70
 Embedded Flash File System (EFFS)
  Upgraded EFFS to release 3.2.2
 Deployment Tools
  All PC utilities that communicate with the serial port interface now support comm port numbers higher than 9

Version 2.1:
  Fixed issue with ARP requests being made while in debug mode for the following platforms:
      CB34EX, MCF5208, MCF5275, MOD5234, MOD5270, MOD5272, MOD5282, PK70, SB70, SB72 and SB72EX.
  Changed documentation format from chm to PDF and reorganized the /Nburn/doc directory.

Version 2.0:
  Added the NBTime Library and Documentation.
  Added MOD5234 Support and Documentation.
  Added additional functions (and supporting documentation) to the NetBurner Runtime Libraries.
  Added NBEclipse (MinGW) IDE, Tools, Debugger, and Documentation.
  Removed Insight GUI.

Version 1.99:
   Added security to IP Setup.
   Modified the MOD5213 Libraries, now the RTOS code is not linked in the NoRtos case. Note: The resultant application is not 800 bytes.
   Added a flags object to the NetBurner UCOS release.
   Added FAT file system support for SD Cards and Compact Flash Cards (MOD5282, MOD5234, MOD5270, and MOD5272 only).
   Added a pins class (Mod5213, MOD5234, MOD5282, MOD5270, and MOD5272 only).
   Added CHAP to PPP.
   Updated CAN driver for Mod5213.
   Added I²C Multimaster IRQ driver for Mod5213.
   Added CB34EX Support and Documentation.
   Added ModL2E Support and Documentation.
   Added SB72EX Support and Documentation.
   Fixed more Documentation Bugs.

Version 1.98:
   Added Mod5213 Support and Documentation.
   Added Network Debugger (all platforms except CFV2-40 and Mod5213).
   Fixed a problem with the network debug stub (all platforms except CFV2-40 and Mod5213).
   Fixed slow single step problem w/ network debugging (all platforms except CFV2-40 and Mod5213).
   Added WiFi support for Mod5270.
   Added SB70 Support and Documentation.
   Fixed more Documentation Bugs.

Version 1.97:

  Upgrade of GNU C/C++ compiler from 3.3.1 to 3.4.2.
   Added Documentation for SmartTrap, TaskScan, uC/OS, Send Mail, and FTP Functions.
   Added Documentation for the Serial and Command Libraries
   Added additional functions (and supporting documentation) to the NetBurner Runtime Libraries.
   Added Mod5270 Support and Documentation.

Version 1.96:

   Fixed TCP bug for over 1 failure in 700 simultaneous connection requests on a single socket.
   Fixed PPP ARP ping problem with PPP interface that comes up and down.
   Added additional filler in ping packets to match common host format.
   Fixed DHCP option 55, 3 and 6 for DNS server and Gateway in initial discover message.
   Added dynamic half/full 100Mbit duplex detection and settings on all 10/100 platforms.
   Added Beta Mod5270 release for ColdFire 5270 processor.
   Added Smart Trap functionality for debugging.
   Added Task Scan utility for debugging over a network connection.
   Added smarter serial RS-485 half duplex echo suppression for SB72 and SB72EX.
   Added Platform detection to TCP Autoupdate utility.
   Added FTP daemon stop request function, and additional error detection for FTPD start.
   Modified CAN function to allow mask high/low for Mod5282.

Version 1.95:

   Added Task Scan Tool to the NetBurner tool set.
   Fixed 485 in SB72EX.
   Fixed Arp problems (Fixed UDP Tx and PPP).
   Added support for multiple network interfaces.
   Added WiFi support (Mod5272 and Mod5282).
   Added WiFi examples (Infrastructure and Ad-Hoc).
   Added WiFi documentation to the NNDK User Manual.
   Fixed DHCP bug.
   Added SB72-EX support.
   Added SB72-EX factory example application.
   Added SB72-EX hardware documentation.
   Modified IP Setup and AutoUpdate to support multiple interfaces.
   Made device discovery more robust with lots of modules.
   Fixed several serial Flow control issues with 5272 serial drivers.
   Added specialized fast TCP send mode for no copy send performance.
   Fixed more documentation bugs.

Version 1.90:

   Added a new version of the GCC compiler - Rev 3.2.3.
   Added NetBurner's Dev C++ IDE.
   Better optimization and performance.
   Added support for the Standard Template Library.
   Added support for C++ I/O cout and cin.
   Added cache support for the Mod5282.
   Added two new functions to the DHCP Client Library.
   TCP performance enhancements.
   Several TCP bug fixes.
   DHCP timeout bug fix.
   New HTML download example.
   Fixed more documentation bugs.

Version 1.83:

   Added Application Identification for IP Setup Tool and AutoUpdate Find.
   Fixed more documentation bugs.

Version 1.82:

   Added new Mod5282 support package and monitor to prevent possible flash memory overwrites of monitor program.
    Added Mod5282 Factory Demo Example
    Added Mod5272 Factory Demo Example
    Added support for the new Ethernet physical layer chips. (Required for Mod5282 revision 1.02.)
    Documentation corrections for Mod5272 and Mod5282 memory maps.
    Mod5282 Ethernet Driver bug fixed.
    Mod5282 CAN Driver bug fixed.
    Fixed more documentation bugs.

Version 1.81:

    Added the NetBurner Mod5282 I/O Board RTC Library Module.
    Added additional Mod5282 code.
    Added an A/D Example Program for the Mod5282.
    Added a RTC Example Program for the Mod5282.
    Added a LED Display Example Program for the Mod5282.
    Added a GPIO Example Program for the Mod5282.
    Added a PITR Example Program for the Mod5282.
    Fixed more documentation bugs.

  Version 1.80:

    Fixed install errors with binary evaluation releases.
    Fixed a TCP bug involving RTOS and Critical sections.
    Cleaned up TCP re-transmit logic.
    Fixed a PPP bug.
    Fixed Multicast on Mod5272 and Mod5282.
    Added Mod5282 support.
    Added Mod5282 documentation.
    Added Mod5272 documentation.

Version 1.79:

    Updated the Insight debugger with a more stable release.
    Fixed AutoUpdate so it will give you the ability to update SB72 with SB72-512.
    Fixed TCP MSS size to maximize performance.
    Fixed TCP priority race condition.
    Changed documentation format from HTML to CHM .

Version 1.78:

    Add a new Application Generation wizard.
    Fixed TCP Retransmit bug so it does not time out when sending lots of small packets.
    Fixed library bug so iprintf and printf support long variables.
    Improved installation so it works better when installing over old installations.
    Improved both the IPSETUP and AutoUpdate.
    Added SB72-512 large SB72 support.
    Modified the TCP stack to help support add ons like SSL.
    Modified the document system to support add on documentation.
    Added the ability to have a multihomed device.

Version 1.77:

    Added Help on using GDB.
    Added GDB demo program to examples.
    Added NTP client program to examples.
    Improved the robustness and functionality of the debugger.
    Added name specification capability to DHCP.
    Added SB72 serialburner example application.
    Added Object Code only (i.e. no source) low cost evaluation capability.
    Fixed a 5272 SB72 Ethernet bug.
    Fixed a multithread select bug.

Version 1.76:

    Fixed a DEBUG build problem with SNMP.
    Fixed a TCP retransmit and Listen overflow bugs.
    Fixed a build problem with the tools on windows XP.

Version 1.75:

    Fixed a 5272 ethernet driver problem.
    Added trap support to the SNMP system.
    Added platform type in the IPSETUP packets.
    Modified IPSETUP and AutoUpdate to use platform type.
    Fixed an ARP problem on busy networks.
    Fixed a build problem with the tools on windows XP.

Version 1.74:

    Fixed a RTOS problem with interrupts in cfinter.h.
    Fixed a DHCP negotiation problem with some DHCP servers.
    Fixed an Ethernet driver problem in the CFV2-66 ethernet driver.
    Fixed a TCP close retransmit problem.
    Fixed a TCP seq rollover problem on retransmit .
    Added support for SB72 platform.

Version 1.73:

    Fixed several SNMP bugs.
    Fixed TCP connect problem.

Version 1.72:

    Added FTP capability see:FTP Client and FTP Server.
    Added additional TCP information functions.

Version 1.71:

    Fixed several SNMP bugs.
    Fixed command processor error handling.
    Fixed CFV2-40I485 ethernet driver buffer overflow bug.

Version 1.70:

    Fixed several linker problems associated with memory size. on CFV2-66.
    Added MPEG file type to html compress and decompress.
    Added HTML password example application.

Version 1.69:

   Improved TCP performance.
        *  CFV2-40 is now capable of 750K bytes/sec TCP performance.
        *  CFV2-66 is now capable of 1.5M bytes/sec TCP performance.
   Added BETA SNMP support (extra cost option).
   Fixed CFV2-66 memory size problem.
   Fixed CFV2-66 Ethernet bug.
   Fixed Local IP Loopback operation.
   Fixed CFV2-40I485 Buffer overrun Ethernet Bug.
   Added Platform definition to compile time predefined symbols.
        *  See an Example of this in the TicTacToe example program look for #ifdef CFV2_66.

Version 1.68:

   Modified environment to better handle multiple target systems.
   Added IGMP V1 (RFC1112) and V2 (RFC 2236) support.

Version 1.67:

    Added POP3 mail capabilities.
    Fixed a volatile bug in select logic.

Version 1.66:

    Fixed ARP problem on Large networks.

Version 1.65:

    Cleaned up some documentation.
    Worked on the reliability of the TCP stack.
    Fixed several timeout and re-transmission problems.
    Added serial burner example code.
    Added the Insight source level debugger.

Version 1.64 (never really released):

    Cleaned up some documentation.
    Fixed GDB stub bug.
    Added a new demo application.
    Rebuilt compiler and Newlib with latest sources.
    Added a "Mail Sample" sample application.
    Added time of reception to ethernet driver.
    Made build modification to work with Linux.
    Fixed TCP Receive Bug.

Version 1.63:

    Fixed buffer starvation problem with TCP on slow links.
    Added DMA registers to sim5206e.h
    Fixed a DNS bug with aliased responses.
    Added the ability to log what is on the screen to the mttty utility.
    Added NoWait version of all the UCOS primitives.
    Added a NoWait version of Select.
    Fixed a Nasty 802.3 Ethernet driver bug.
    Improved interrupt latency by removing extra locks.
    Added sbrk to bsp.c to fix a malloc bug.
    Improved buffer management code.
    See the Revision history.

Version 1.62:

    Added 802.3 Encapsulation.
    Added BOOTP support.
    Fixed an ARP and PPP bugs.
    Cleaned up headers to work with straight 'C'.
    See the Revision history.

Version 1.61:

    Added HTTP password support.
    Fixed several TCP and Ethernet bugs.
    Restructured the code to help support different ColdFire hardware platforms.
    See the Revision history.

Version 1.60:

    Changed the 2.95 version of GCC/EGCS.
    Converted the Object format to ELF not COFF so we are compatible with more third party debuggers.
    Added support for DHCP.
    Added support for the GNU GBS debugger
    Added some diagnostics notes.

Version 1.53:

    Changed the 2.95 version of GCC/EGCS.
    Added support for expansion FD type devices like the external Serial board.
    Fixed more documentation bugs.
    Fixed a Buffers bug that caused corruption when socket connections where aborted.

Version 1.52:

    Fixed a TCP bug that was causing the system to crash when it received RST packets on a busy network.
    Fixed some bugs in the sample code and documentation related to source control corrupting gif and pdf files.

Version 1.51:

    PPP for both connection initiation and call answering using a standard AT command set Modem.
    Send Mail - The ability to send E-Mail from the NetBurner board, using any Send Mail server.
    Telnet Command processing.
    Simple DNS.
    Code Update - The ability to update running code from any PC over the network.
    Bug Fixes.

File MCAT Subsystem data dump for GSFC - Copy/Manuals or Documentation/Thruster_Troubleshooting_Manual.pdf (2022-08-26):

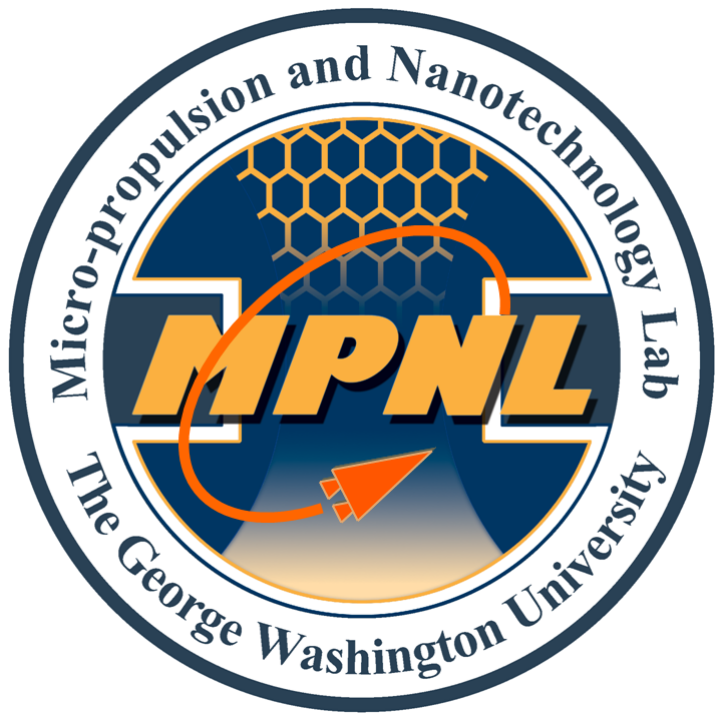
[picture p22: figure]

The George Washington University

# Thruster Troubleshooting Manual

### Author: Joseph Lukas

### Advisor: Dr. Michael Keidar

### March 16, 2015

## I Introduction

This document will contain all the steps necessary for thruster troubleshooting including: applying carbon paint, finding the correct resistance values between the anode and cathode and fixing a loose anode ring terminal.

## Contents

I Introduction | 1

## II Loose Anode Ring Terminal

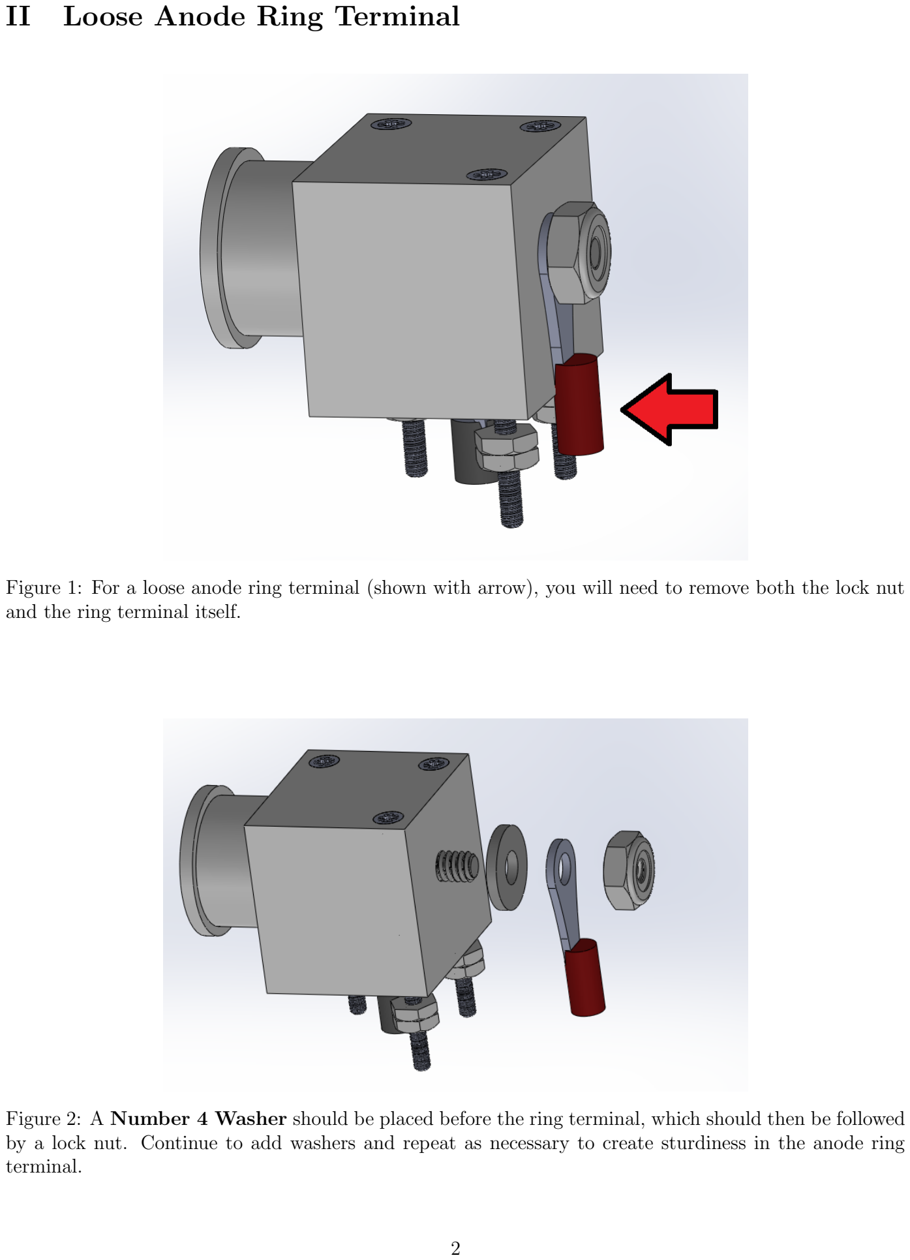
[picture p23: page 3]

Figure 1: For a loose anode ring terminal (shown with arrow), you will need to remove both the lock nut and the ring terminal itself.

Figure 2: A Number 4 Washer should be placed before the ring terminal, which should then be followed by a lock nut. Continue to add washers and repeat as necessary to create sturdiness in the anode ring terminal.

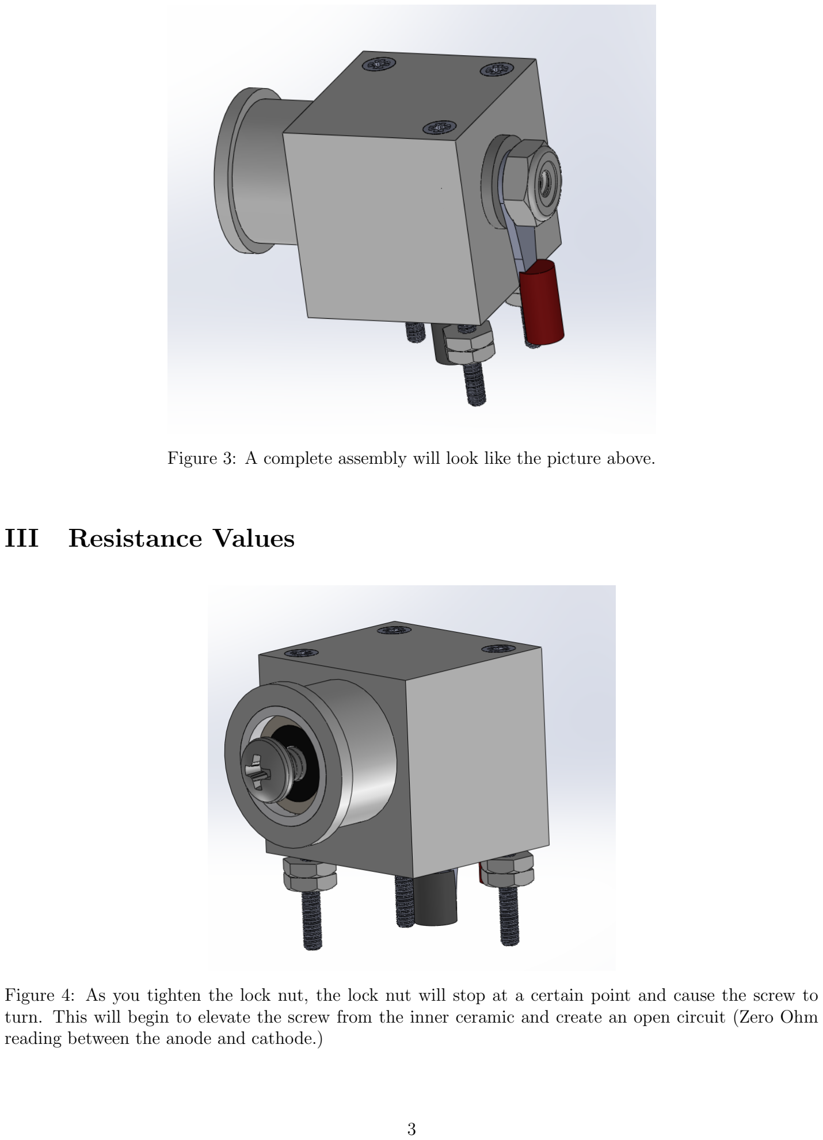
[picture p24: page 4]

Figure 3: A complete assembly will look like the picture above.

## III Resistance Values

Figure 4: As you tighten the lock nut, the lock nut will stop at a certain point and cause the screw to turn. This will begin to elevate the screw from the inner ceramic and create an open circuit (Zero Ohm reading between the anode and cathode.)

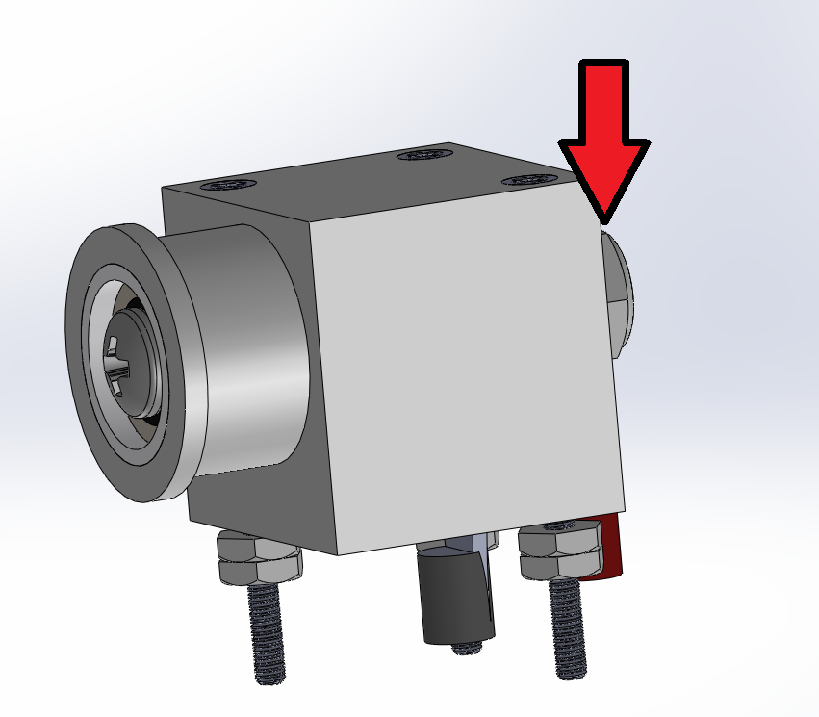
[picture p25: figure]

Figure 5: To tighten the screw back in place, you will need to hold the lock nut (shown with arrow) while you turn the screw itself. Tighten until the bottom of the screw head appears flush with the inner ceramic and cathode. From here, you should do a resistance check between the anode and cathode. Typical resistance values for the CANYVAL Thruster should be anywhere between 0.5 kΩ and a few MΩs. An ideal case will be in the kΩ range.

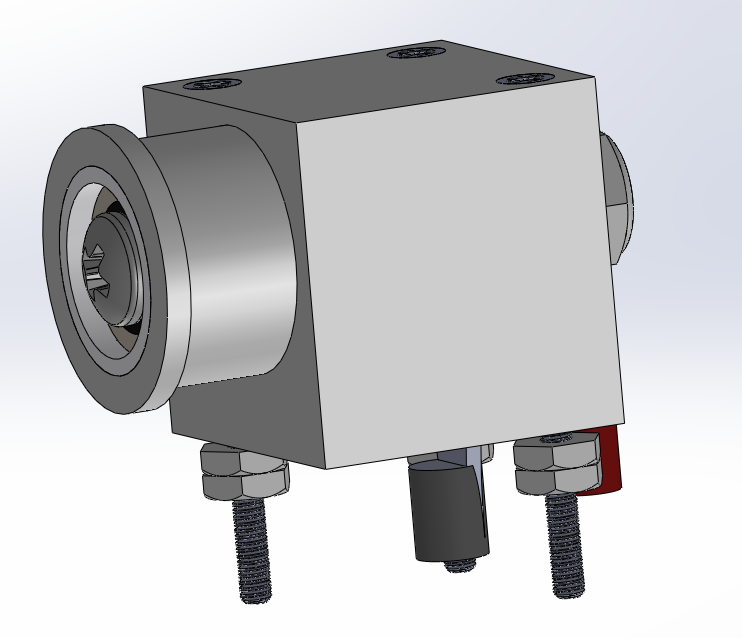
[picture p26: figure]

Figure 6: Turn the screw in quarter turns and measure the resistance until an ideal value is found.

## IV Carbon Paint Application

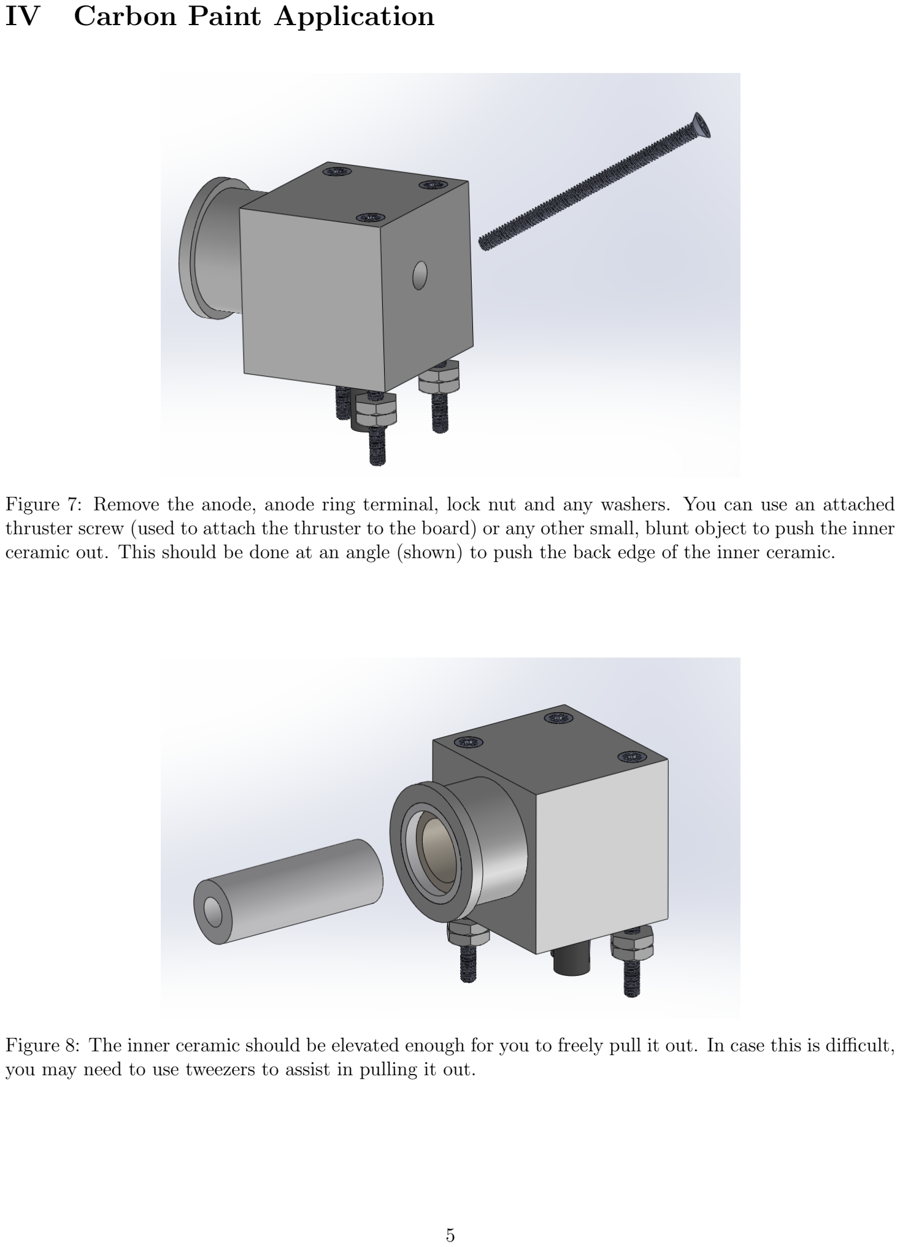
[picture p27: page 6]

Figure 7: Remove the anode, anode ring terminal, lock nut and any washers. You can use an attached thruster screw (used to attach the thruster to the board) or any other small, blunt object to push the inner ceramic out. This should be done at an angle (shown) to push the back edge of the inner ceramic.

Figure 8: The inner ceramic should be elevated enough for you to freely pull it out. In case this is difficult, you may need to use tweezers to assist in pulling it out.

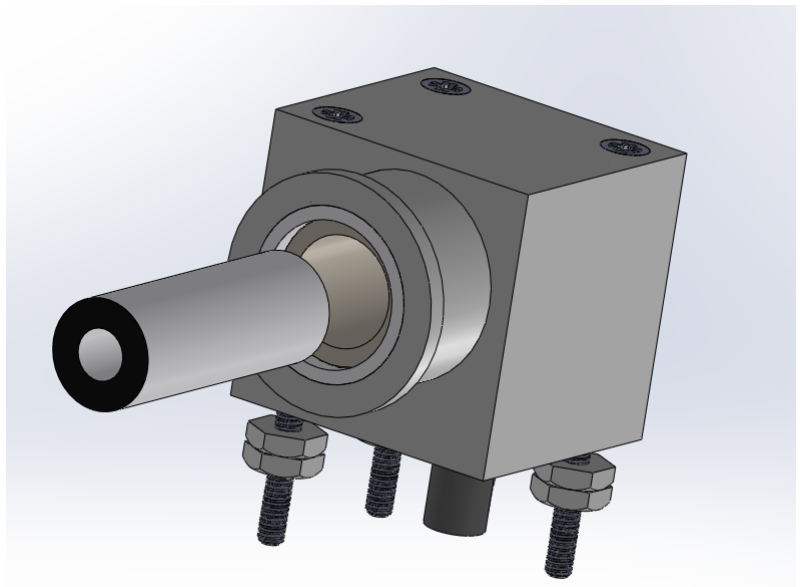
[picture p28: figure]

Figure 9: With the inner ceramic out, apply a thin layer of carbon paint. This should be done using a light brush stroke or a Q-Tip. Allow to dry for 10 to 15 minutes.

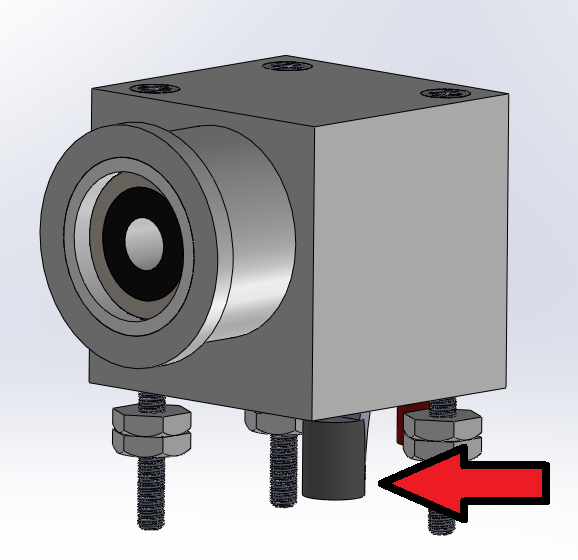
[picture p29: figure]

Figure 10: To push the ceramic back in, you should be able to press it in with your finger. If trouble arises, use a thin, soft material to press it down until it is flush with the cathode. You may need to adjust the Cathode Ring Terminal (shown with arrow) to allow the inner ceramic to be flush. This involves moving it left and right while pushing the ceramic down.

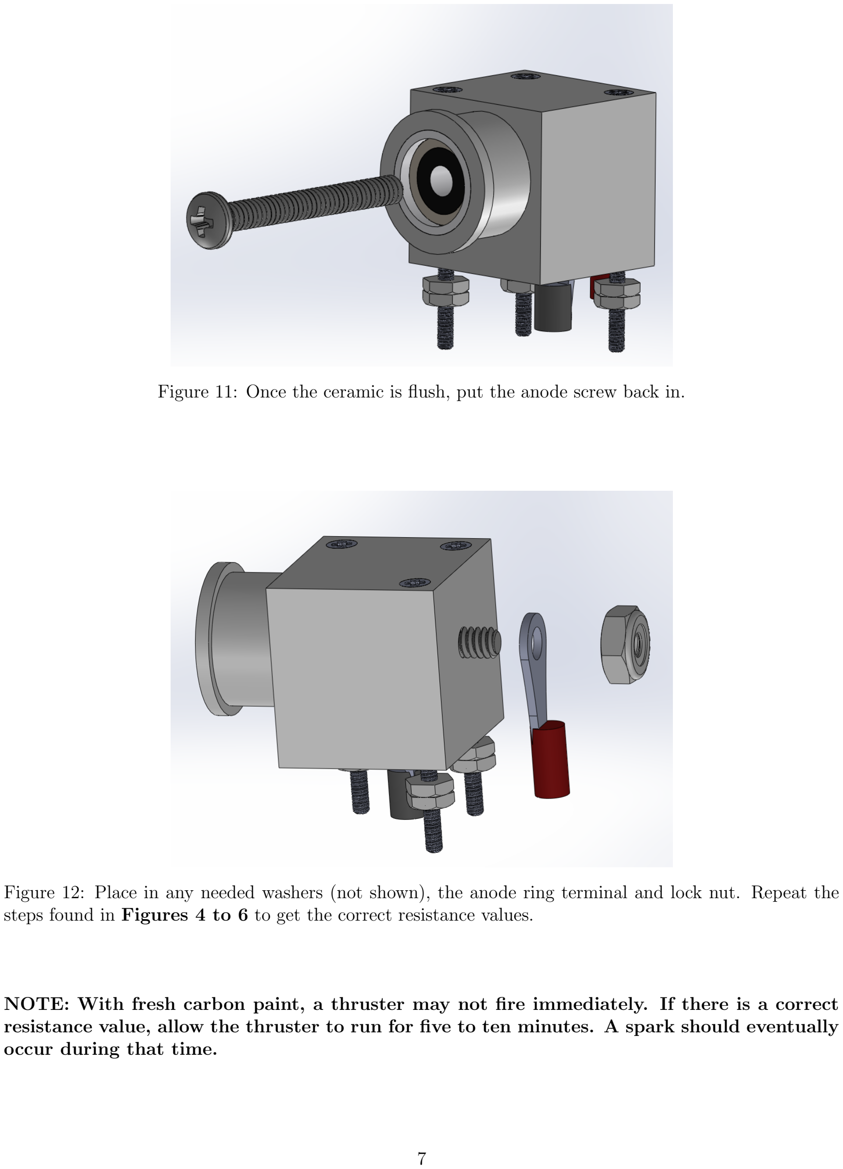
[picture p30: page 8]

Figure 11: Once the ceramic is flush, put the anode screw back in.

Figure 12: Place in any needed washers (not shown), the anode ring terminal and lock nut. Repeat the steps found in Figures 4 to 6 to get the correct resistance values.

NOTE: With fresh carbon paint, a thruster may not fire immediately. If there is a correct resistance value, allow the thruster to run for five to ten minutes. A spark should eventually occur during that time.

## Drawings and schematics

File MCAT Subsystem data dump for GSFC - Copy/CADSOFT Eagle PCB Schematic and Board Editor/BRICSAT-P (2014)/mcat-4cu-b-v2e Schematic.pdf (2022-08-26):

## 2 x ESQ-126-39-G-D

J1

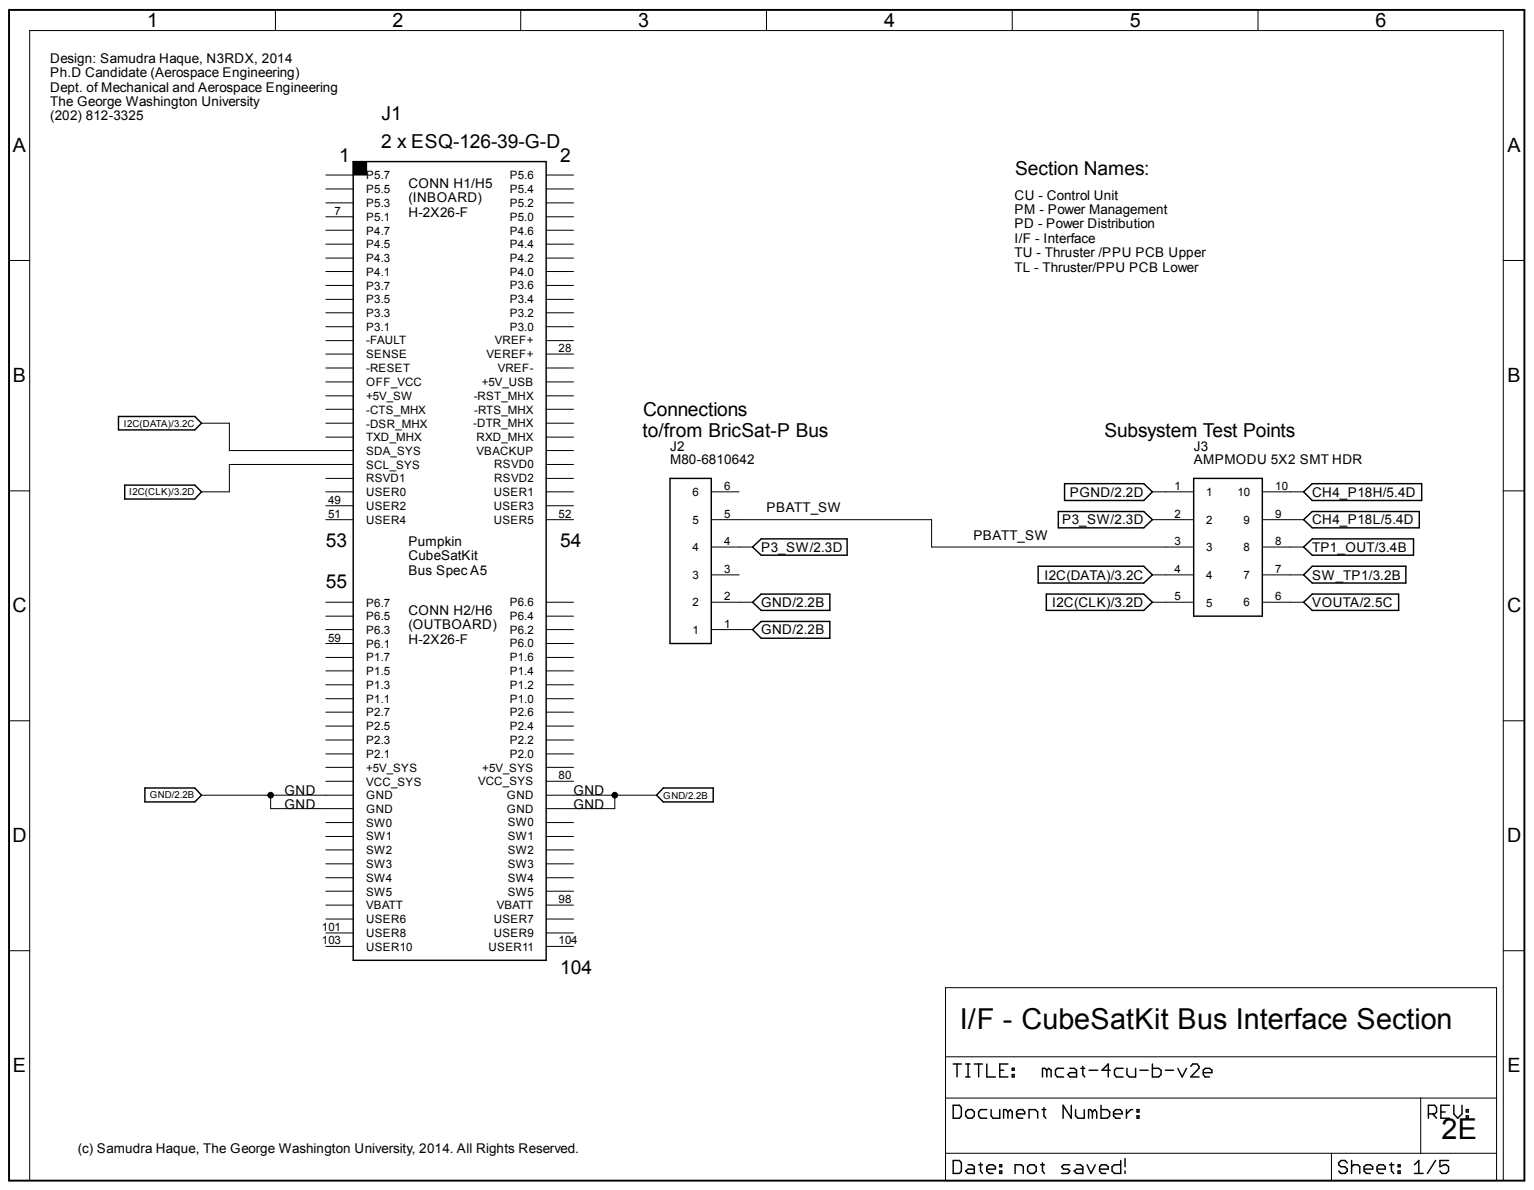
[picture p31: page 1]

Design: Samudra Haque, N3RDX, 2014
Ph.D Candidate (Aerospace Engineering)
Dept. of Mechanical and Aerospace Engineering
The George Washington University

CU - Control Unit
PM - Power Management
PD - Power Distribution
I/F - Interface
TU - Thruster /PPU PCB Upper
TL - Thruster/PPU PCB Lower

I/F - CubeSatKit Bus Interface Section

(c) Samudra Haque, The George Washington University, 2014. All Rights Reserved.

## Switching Regulator f = 300 kHz

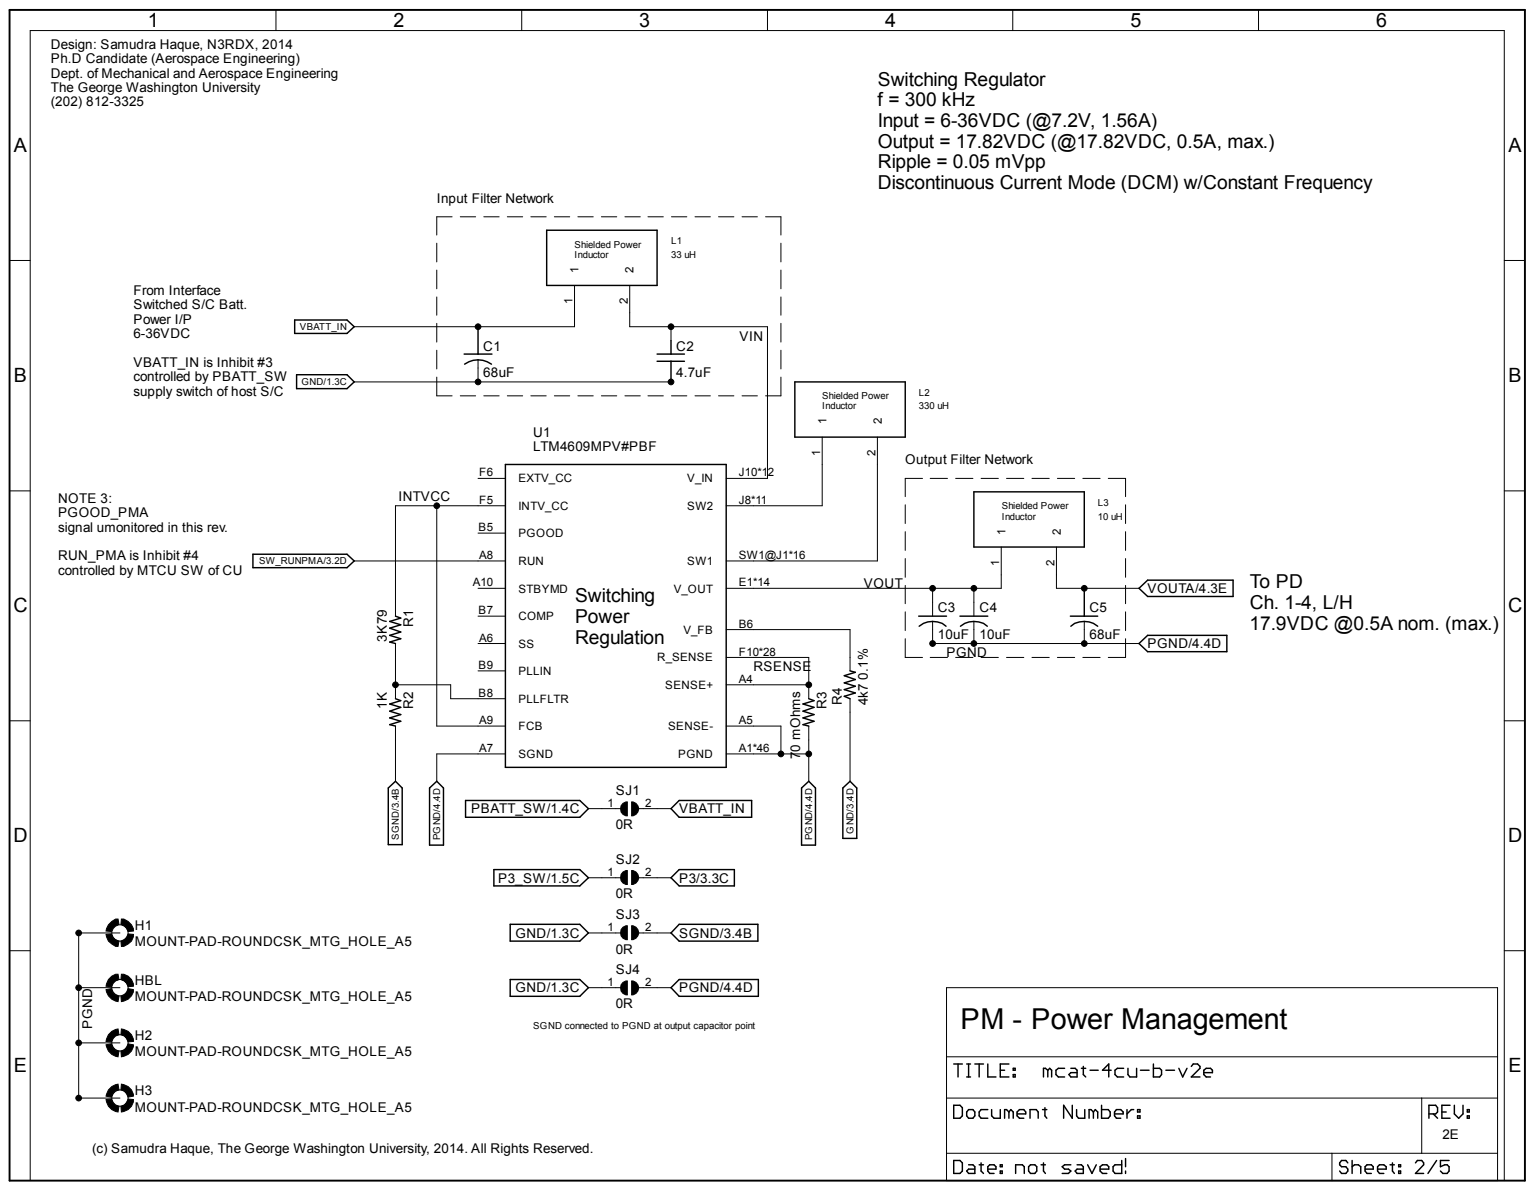
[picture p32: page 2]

Dept. of Mechanical and Aerospace Engineering
The George Washington University

Input = 6-36VDC (@7.2V, 1.56A)
Output = 17.82VDC (@17.82VDC, 0.5A, max.)
Ripple = 0.05 mVpp
Discontinuous Current Mode (DCM) w/Constant Frequency

VBATT_IN is Inhibit #3
controlled by PBATT_SW
supply switch of host S/C

NOTE 3:
PGOOD_PMA
signal umonitored in this rev.

RUN_PMA is Inhibit #4
controlled by MTCU SW of CU

SGND connected to PGND at output capacitor point

A

A

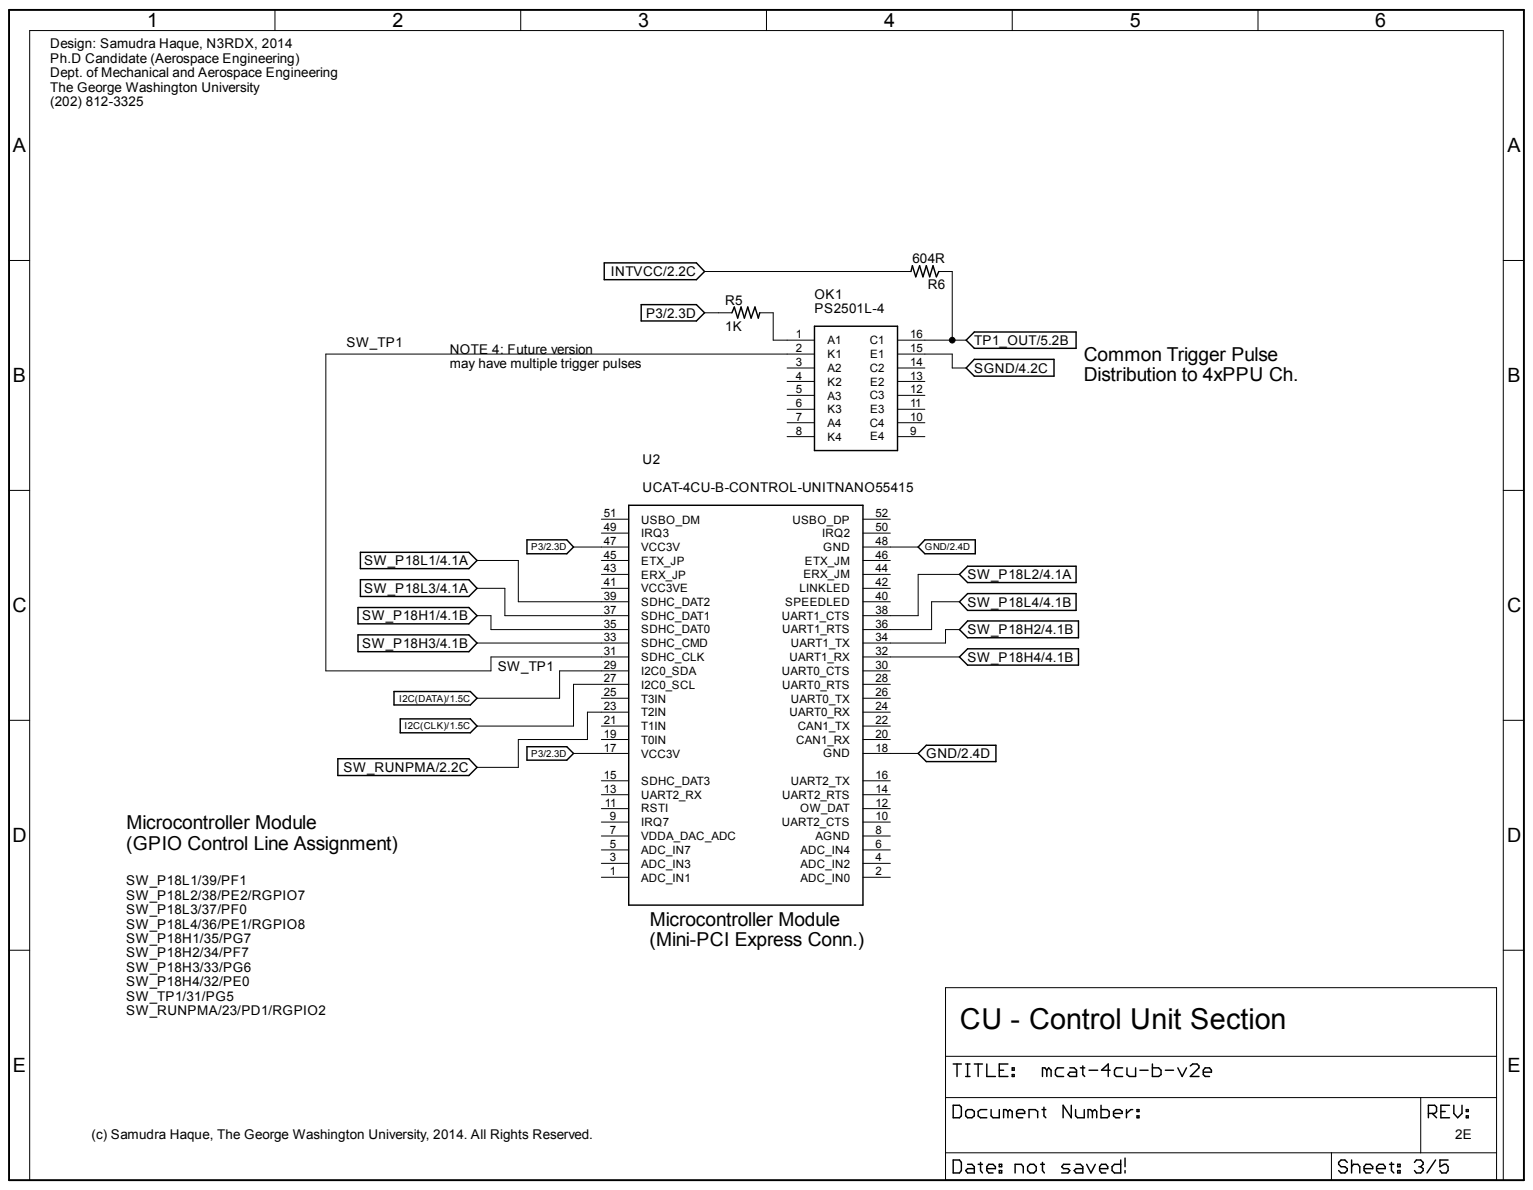
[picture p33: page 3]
SW_P18L1/39/PF1 SW_P18L2/38/PE2/RGPIO7 SW_P18L3/37/PF0 SW_P18L4/36/PE1/RGPIO8 SW_P18H1/35/PG7 SW_P18H2/34/PF7 SW_P18H3/33/PG6 SW_P18H4/32/PE0 SW_TP1/31/PG5 SW_RUNPMA/23/PD1/RGPIO2; UCAT-4CU-B-CONTROL-UNITNANO55415; ADC_IN1 1; ADC_IN0; 2 ADC_IN3 3; ADC_IN2; 4 ADC_IN7 5; ADC_IN4; 6 VDDA_DAC_ADC 7; AGND; 8 IRQ7 9; UART2_CTS; 10 RSTI 11; OW_DAT; 12 UART2_RX 13; UART2_RTS; 14 SDHC_DAT3 15; UART2_TX; VCC3V 17; GND; CAN1_RX; CAN1_TX; UART0_RX; I2C0_SCL 27; UART0_TX; I2C0_SDA 29; UART0_RTS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

The George Washington University

NOTE 4: Future version
may have multiple trigger pulses

Common Trigger Pulse
Distribution to 4xPPU Ch.

Microcontroller Module
(GPIO Control Line Assignment)

(Mini-PCI Express Conn.)

CU - Control Unit Section

A

A

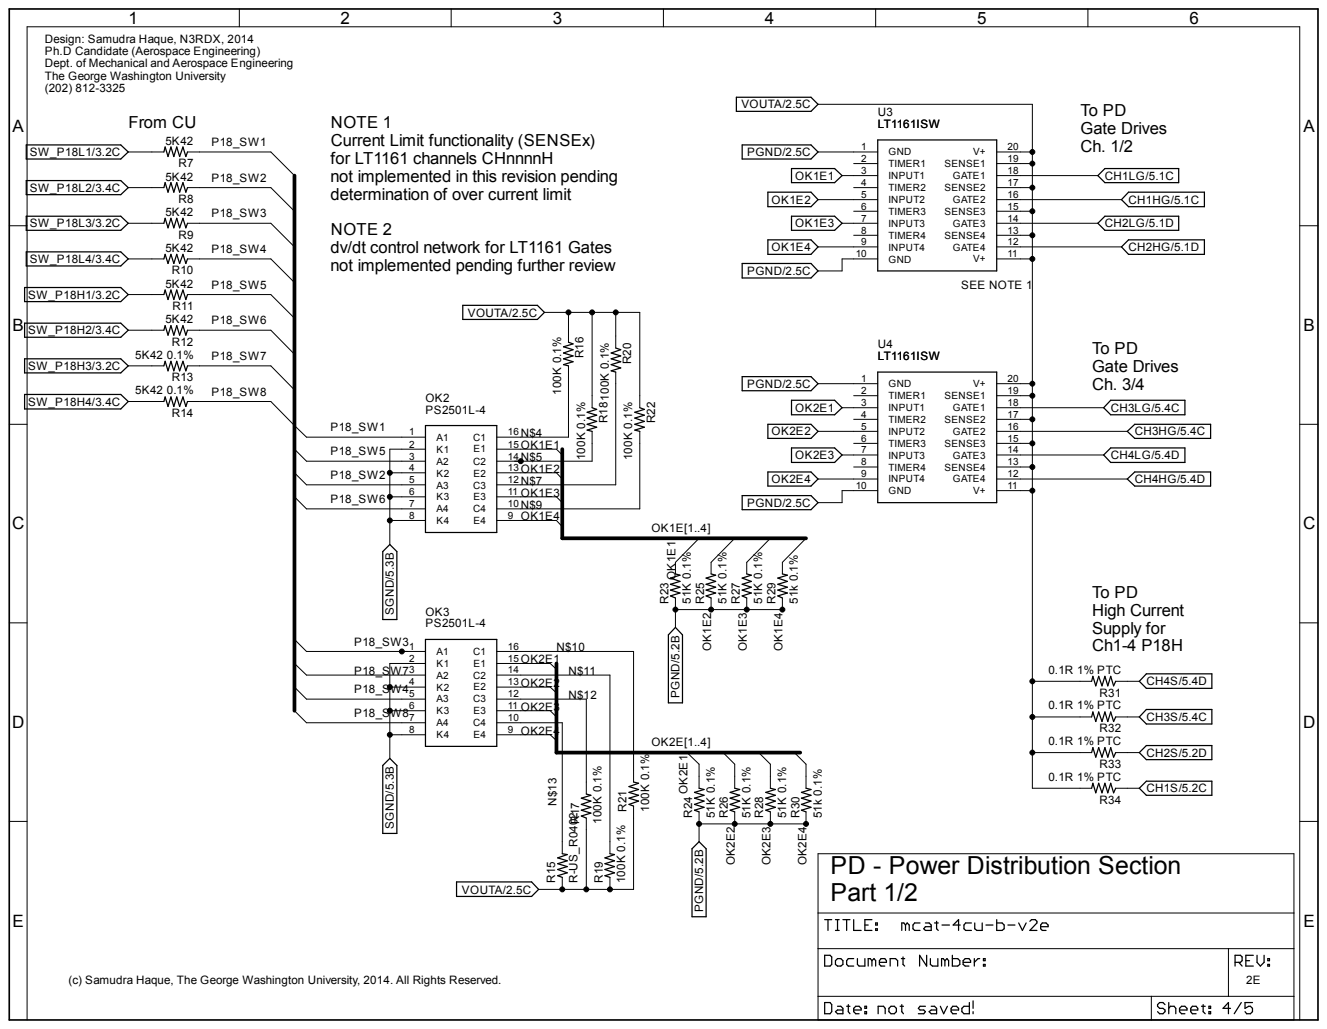
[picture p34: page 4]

The George Washington University

NOTE 1
Current Limit functionality (SENSEx)
for LT1161 channels CHnnnnH
not implemented in this revision pending
determination of over current limit

NOTE 2
dv/dt control network for LT1161 Gates
not implemented pending further review

A

A

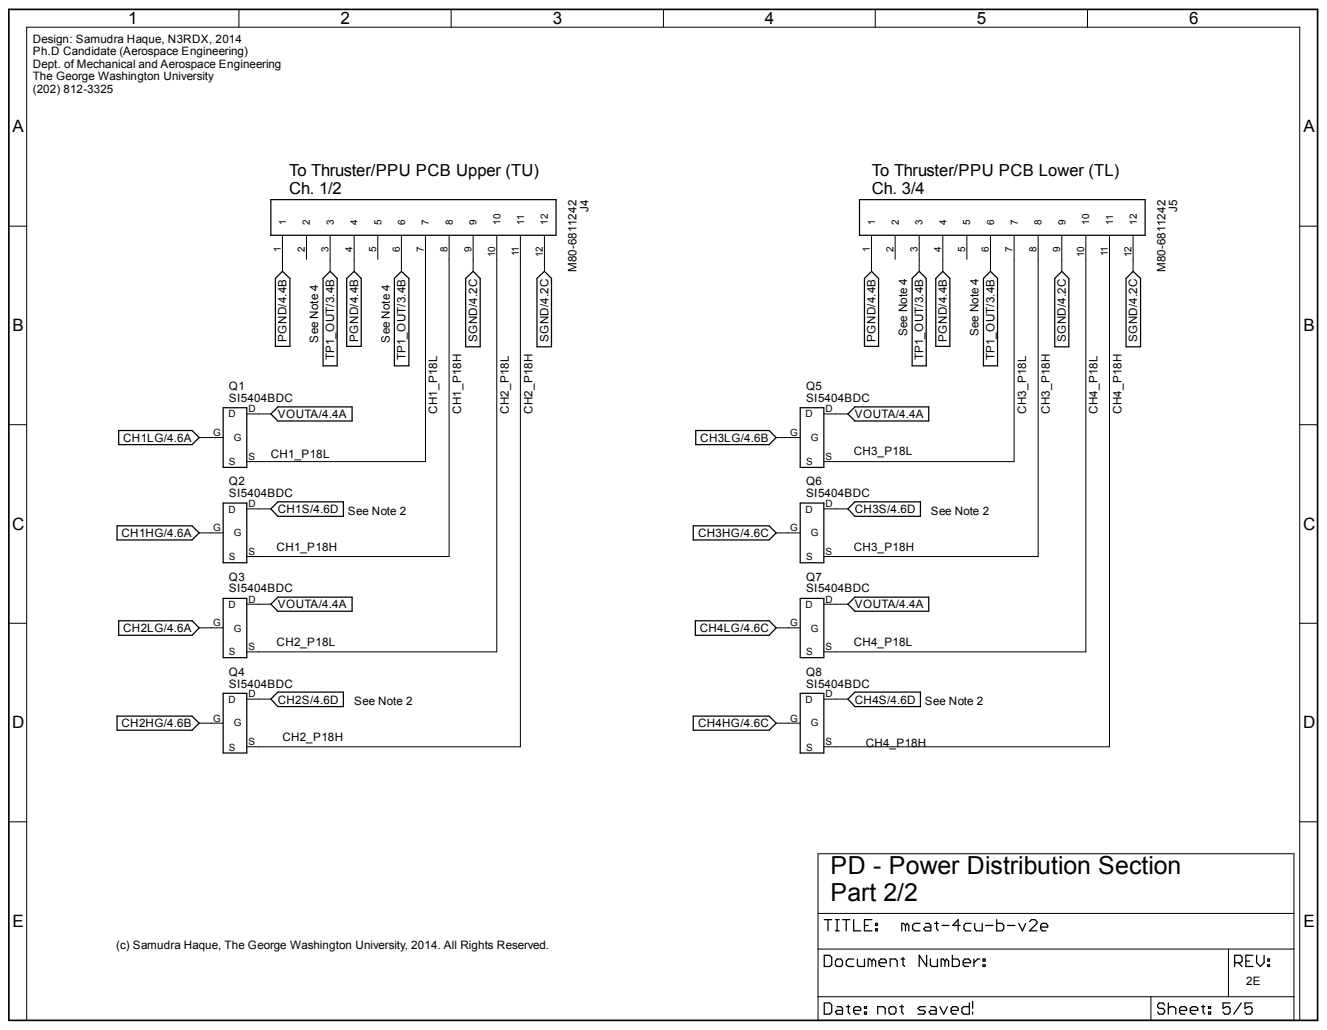
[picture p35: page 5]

The George Washington University

To Thruster/PPU PCB Upper (TU)

To Thruster/PPU PCB Lower (TL)

PD - Power Distribution Section
Part 2/2

(c) Samudra Haque, The George Washington University, 2014. All Rights Reserved.

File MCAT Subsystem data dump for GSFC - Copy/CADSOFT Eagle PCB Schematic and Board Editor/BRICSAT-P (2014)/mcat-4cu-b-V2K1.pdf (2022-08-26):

# MCAT-4CU-B Micro-Cathode Arc Thruster Subsystem 4-Channel Unit Controller PCB Rev. 2K1 | Datecode 201407141434

Warning: Access restricted to permitted users only. Subject to applicable ITAR regulations, if any.

# Designer: Samudra N3RDX, G19124781 Designer Contact: (202) 812-3325

4-layer PCB, 0.062 inches (1.5748 mm), double sided construction.

# For use in US Naval Academy spacecraft BRICSat-P

# Use in conjunction with MCAT-1C-TBT-xxx and MCAT-1C-TBB-xxx by TEEL

(c) George Washington University, 2014. All Rights Reserved.

# Not for public distribution

Document Number: 201407141434 | REV: 2K1
Date: 7/14/2014 2:39:43 PM | Sheet: 1/6

## TITLE:

## mcat-4cu-b-V2K

# Cover Sheet

## Section Names:

A

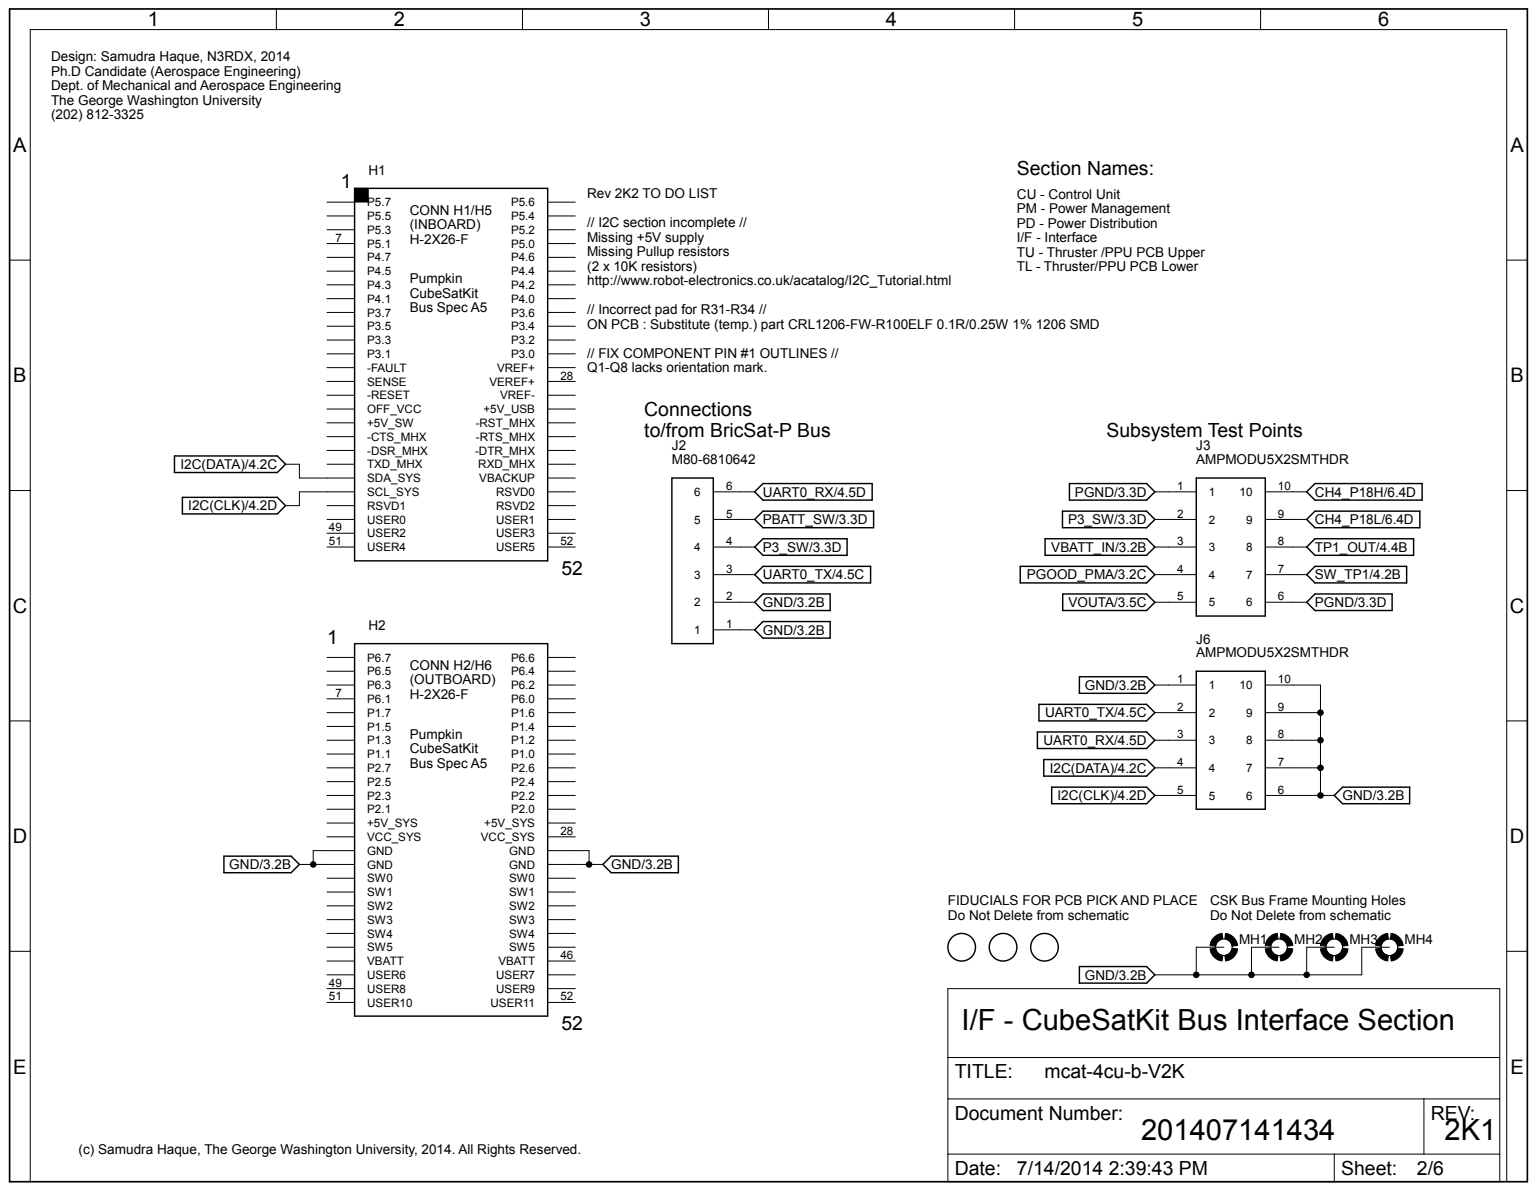
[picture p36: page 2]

Design: Samudra Haque, N3RDX, 2014
Ph.D Candidate (Aerospace Engineering)
Dept. of Mechanical and Aerospace Engineering
The George Washington University

Rev 2K2 TO DO LIST

CU - Control Unit
PM - Power Management
PD - Power Distribution
I/F - Interface
TU - Thruster /PPU PCB Upper
TL - Thruster/PPU PCB Lower

// I2C section incomplete //
Missing +5V supply
Missing Pullup resistors
(2 x 10K resistors)
http://www.robot-electronics.co.uk/acatalog/I2C_Tutorial.html

// Incorrect pad for R31-R34 //
ON PCB : Substitute (temp.) part CRL1206-FW-R100ELF 0.1R/0.25W 1% 1206 SMD

// FIX COMPONENT PIN #1 OUTLINES //
Q1-Q8 lacks orientation mark.

FIDUCIALS FOR PCB PICK AND PLACE
Do Not Delete from schematic

CSK Bus Frame Mounting Holes

I/F - CubeSatKit Bus Interface Section

(c) Samudra Haque, The George Washington University, 2014. All Rights Reserved.

## Switching Regulator f = 300 kHz

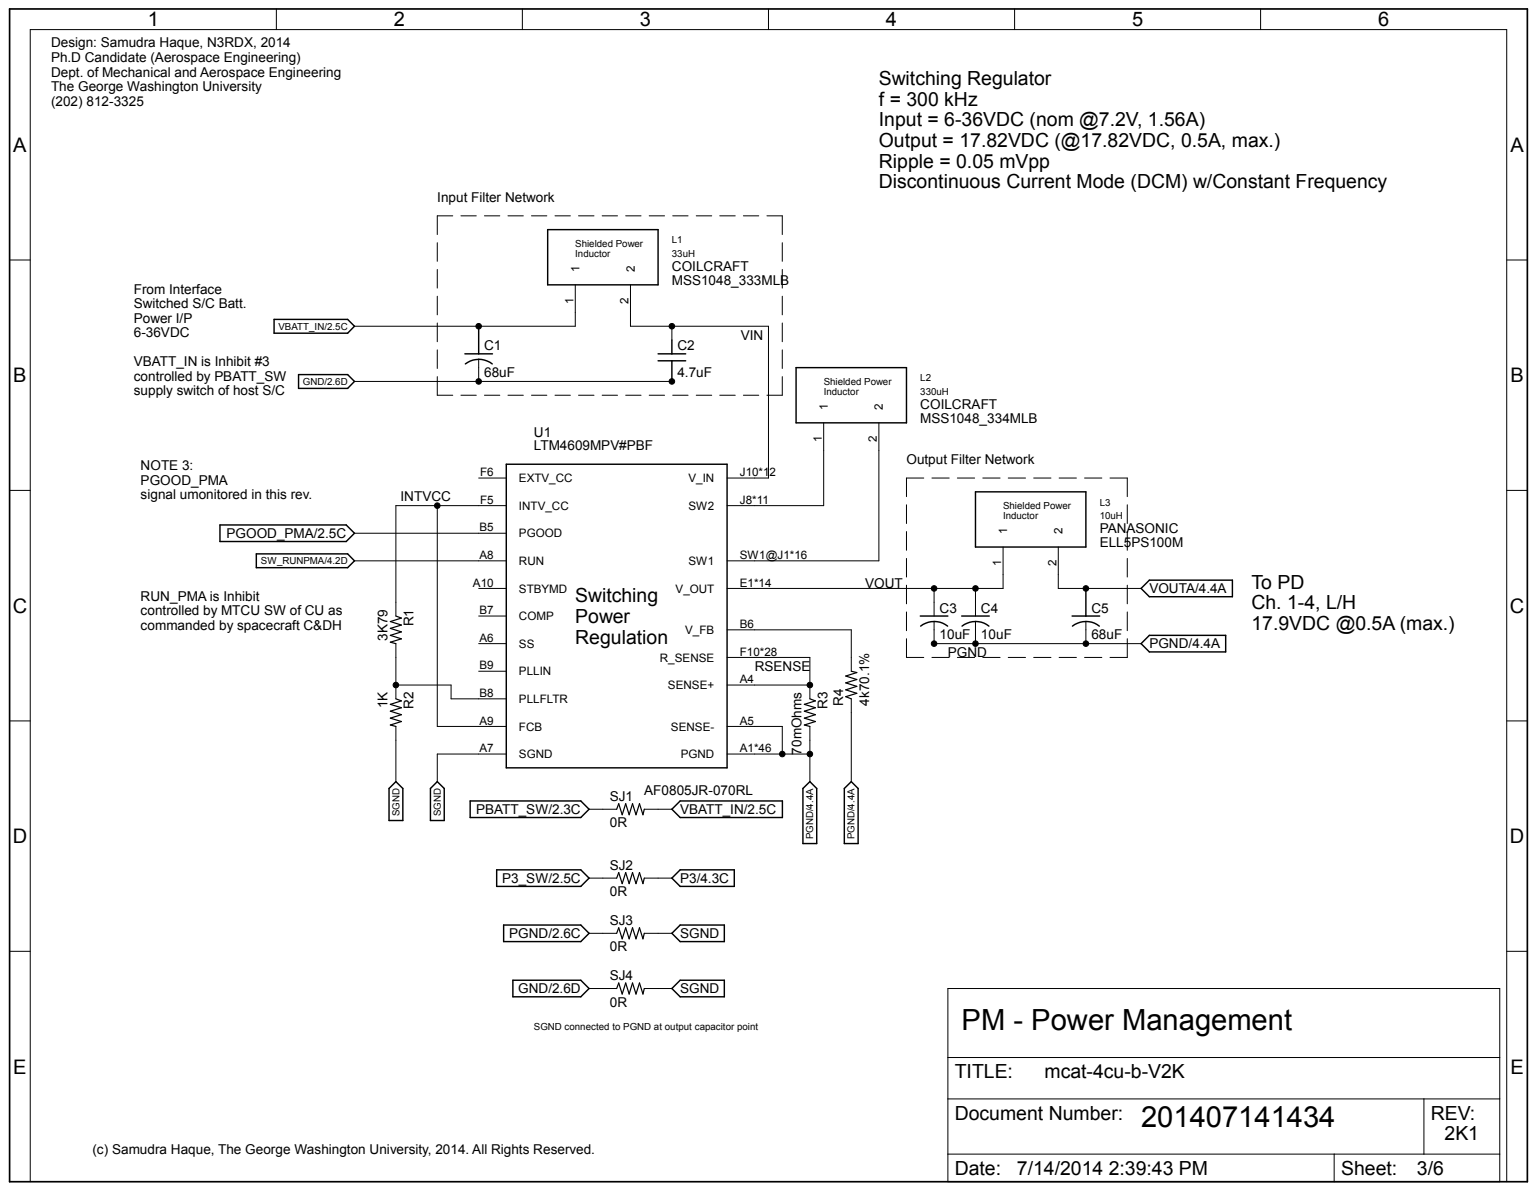
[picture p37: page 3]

The George Washington University

Input = 6-36VDC (nom @7.2V, 1.56A)
Output = 17.82VDC (@17.82VDC, 0.5A, max.)
Ripple = 0.05 mVpp
Discontinuous Current Mode (DCM) w/Constant Frequency

VBATT_IN is Inhibit #3
controlled by PBATT_SW
supply switch of host S/C

NOTE 3:
PGOOD_PMA
signal umonitored in this rev.

RUN_PMA is Inhibit
controlled by MTCU SW of CU as
commanded by spacecraft C&DH

SGND connected to PGND at output capacitor point

A

A

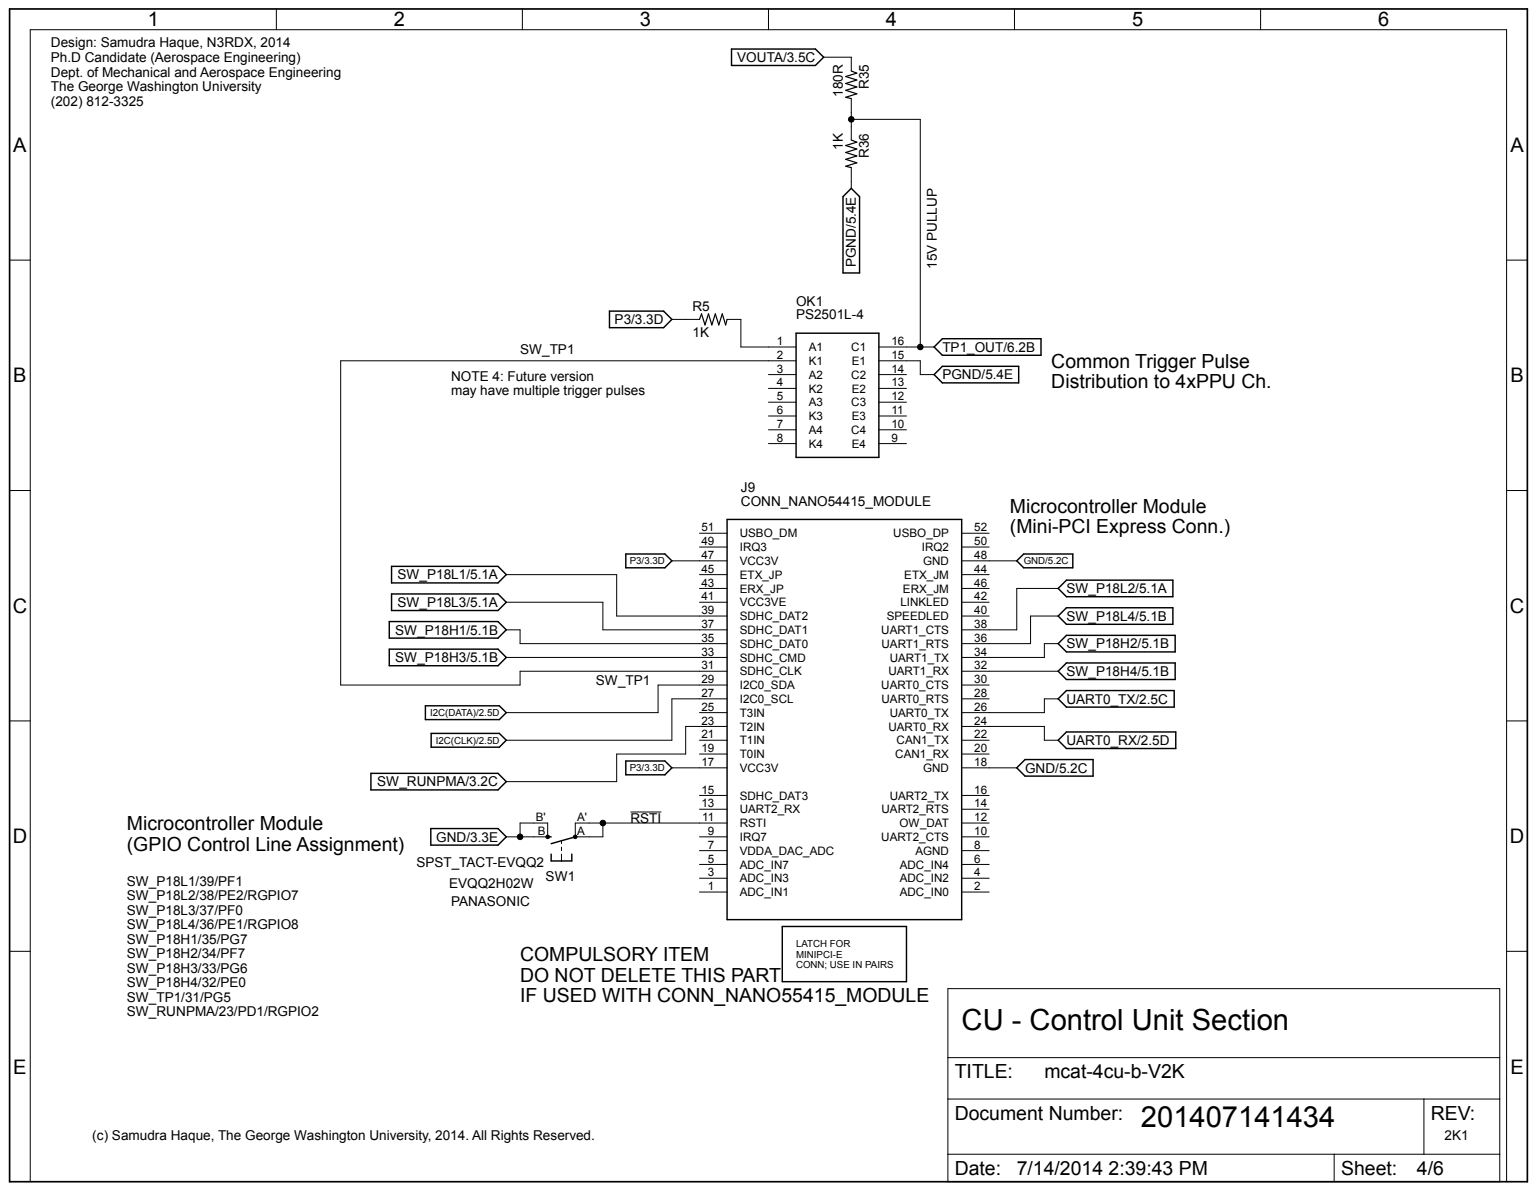
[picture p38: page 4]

Distribution to 4xPPU Ch. NOTE 4: Future version
may have multiple trigger pulses

Microcontroller Module
(Mini-PCI Express Conn.)

(GPIO Control Line Assignment)

COMPULSORY ITEM
DO NOT DELETE THIS PART
IF USED WITH CONN_NANO55415_MODULE

LATCH FOR
MINIPCI-E
CONN; USE IN PAIRS

CU - Control Unit Section

## NOTE 1 Current Limit functionality (SENSEx)

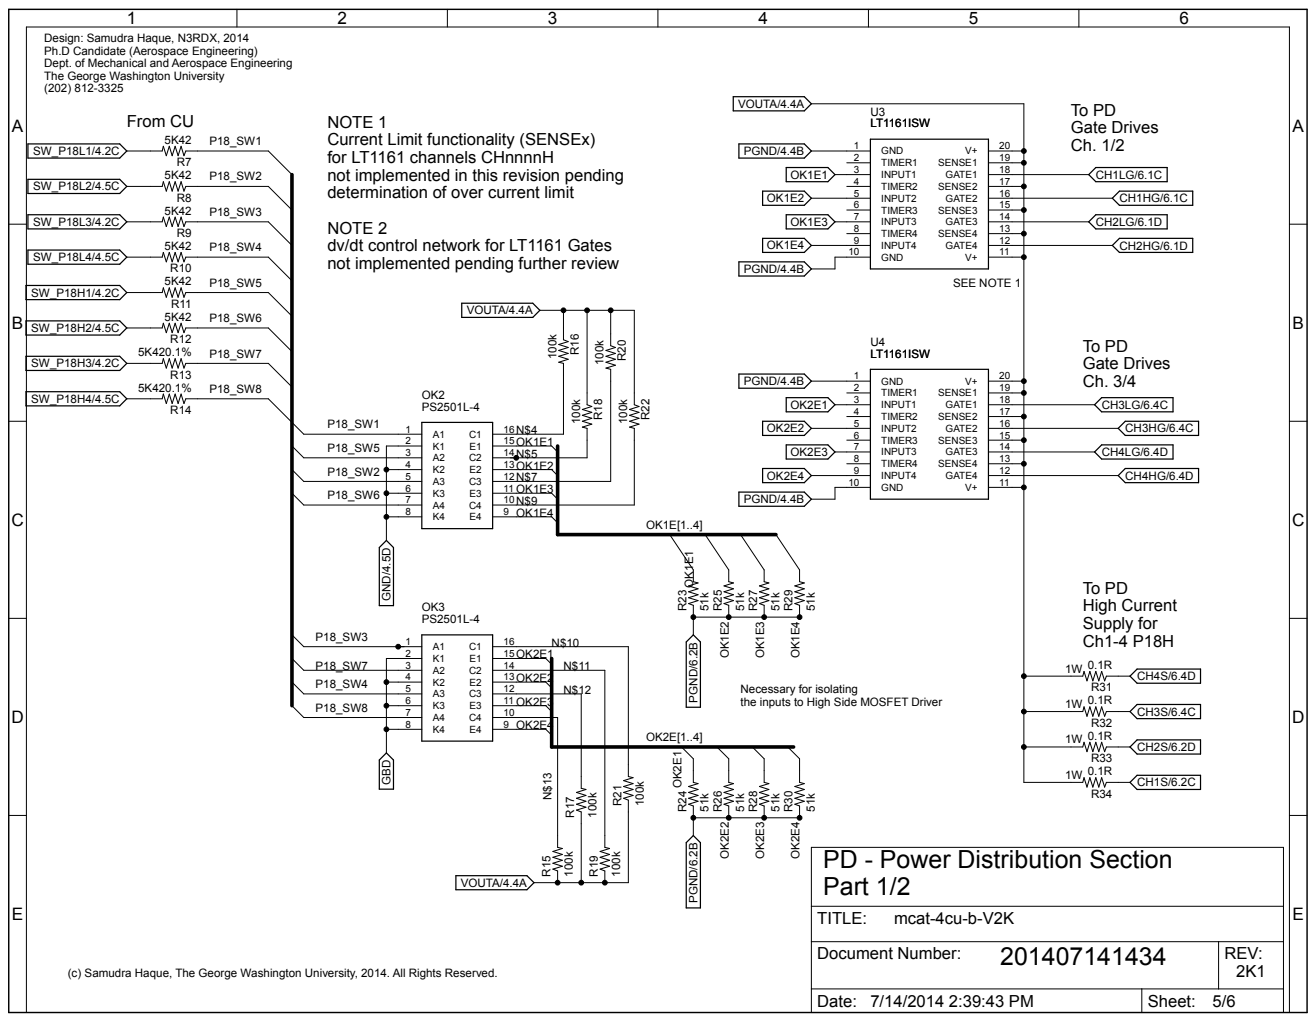
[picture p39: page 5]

for LT1161 channels CHnnnnH
not implemented in this revision pending
determination of over current limit

NOTE 2
dv/dt control network for LT1161 Gates
not implemented pending further review

Necessary for isolating
the inputs to High Side MOSFET Driver

## To Thruster/PPU PCB Upper (TU)

Ch. 1/2

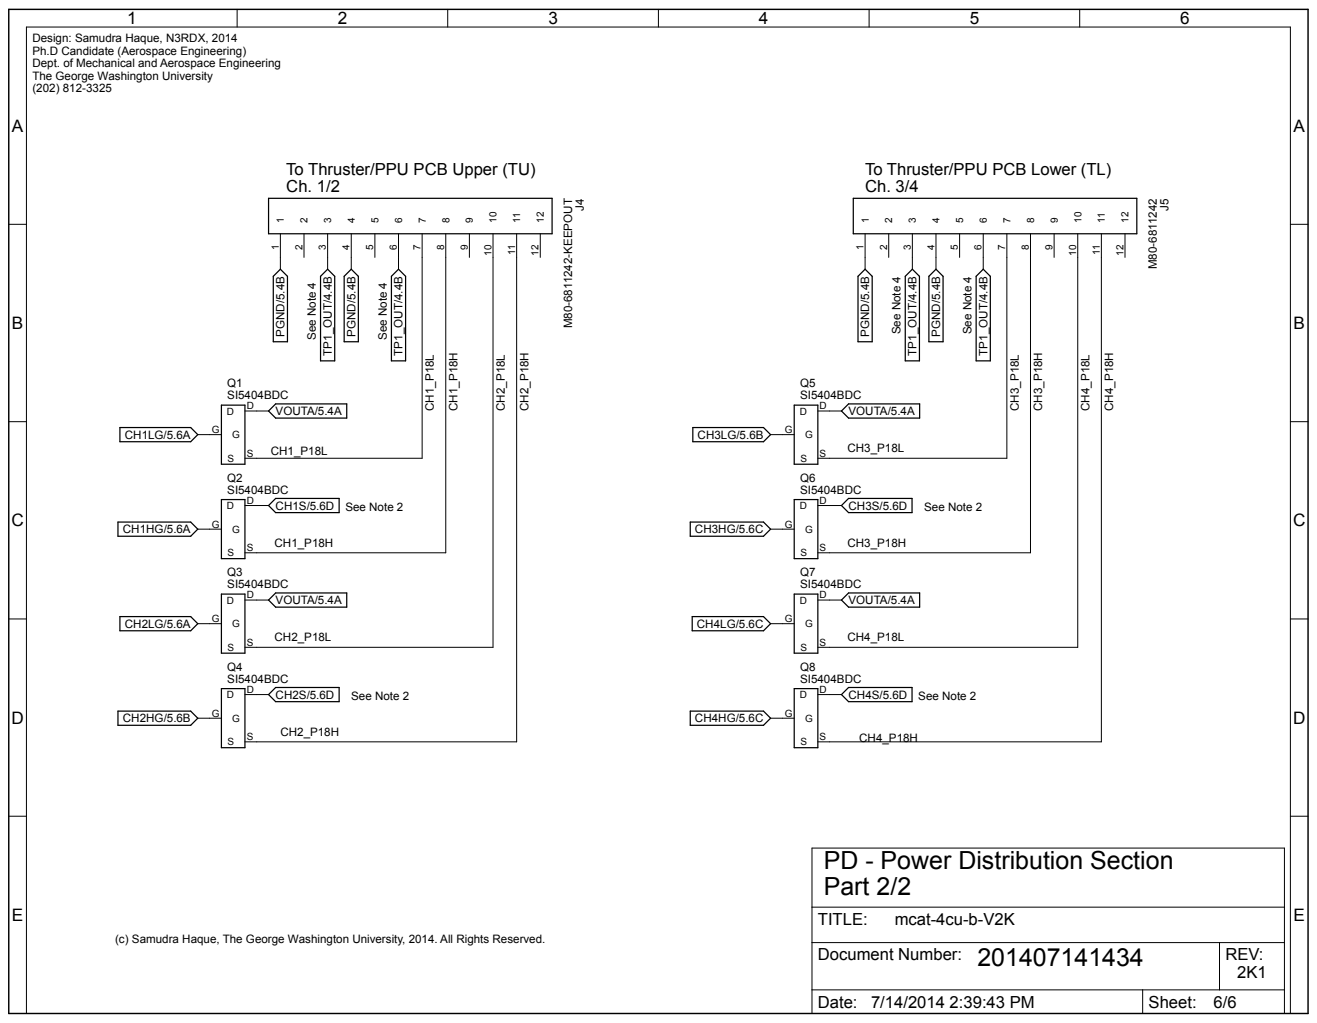
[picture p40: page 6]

To Thruster/PPU PCB Lower (TL)

PD - Power Distribution Section
Part 2/2

(c) Samudra Haque, The George Washington University, 2014. All Rights Reserved.

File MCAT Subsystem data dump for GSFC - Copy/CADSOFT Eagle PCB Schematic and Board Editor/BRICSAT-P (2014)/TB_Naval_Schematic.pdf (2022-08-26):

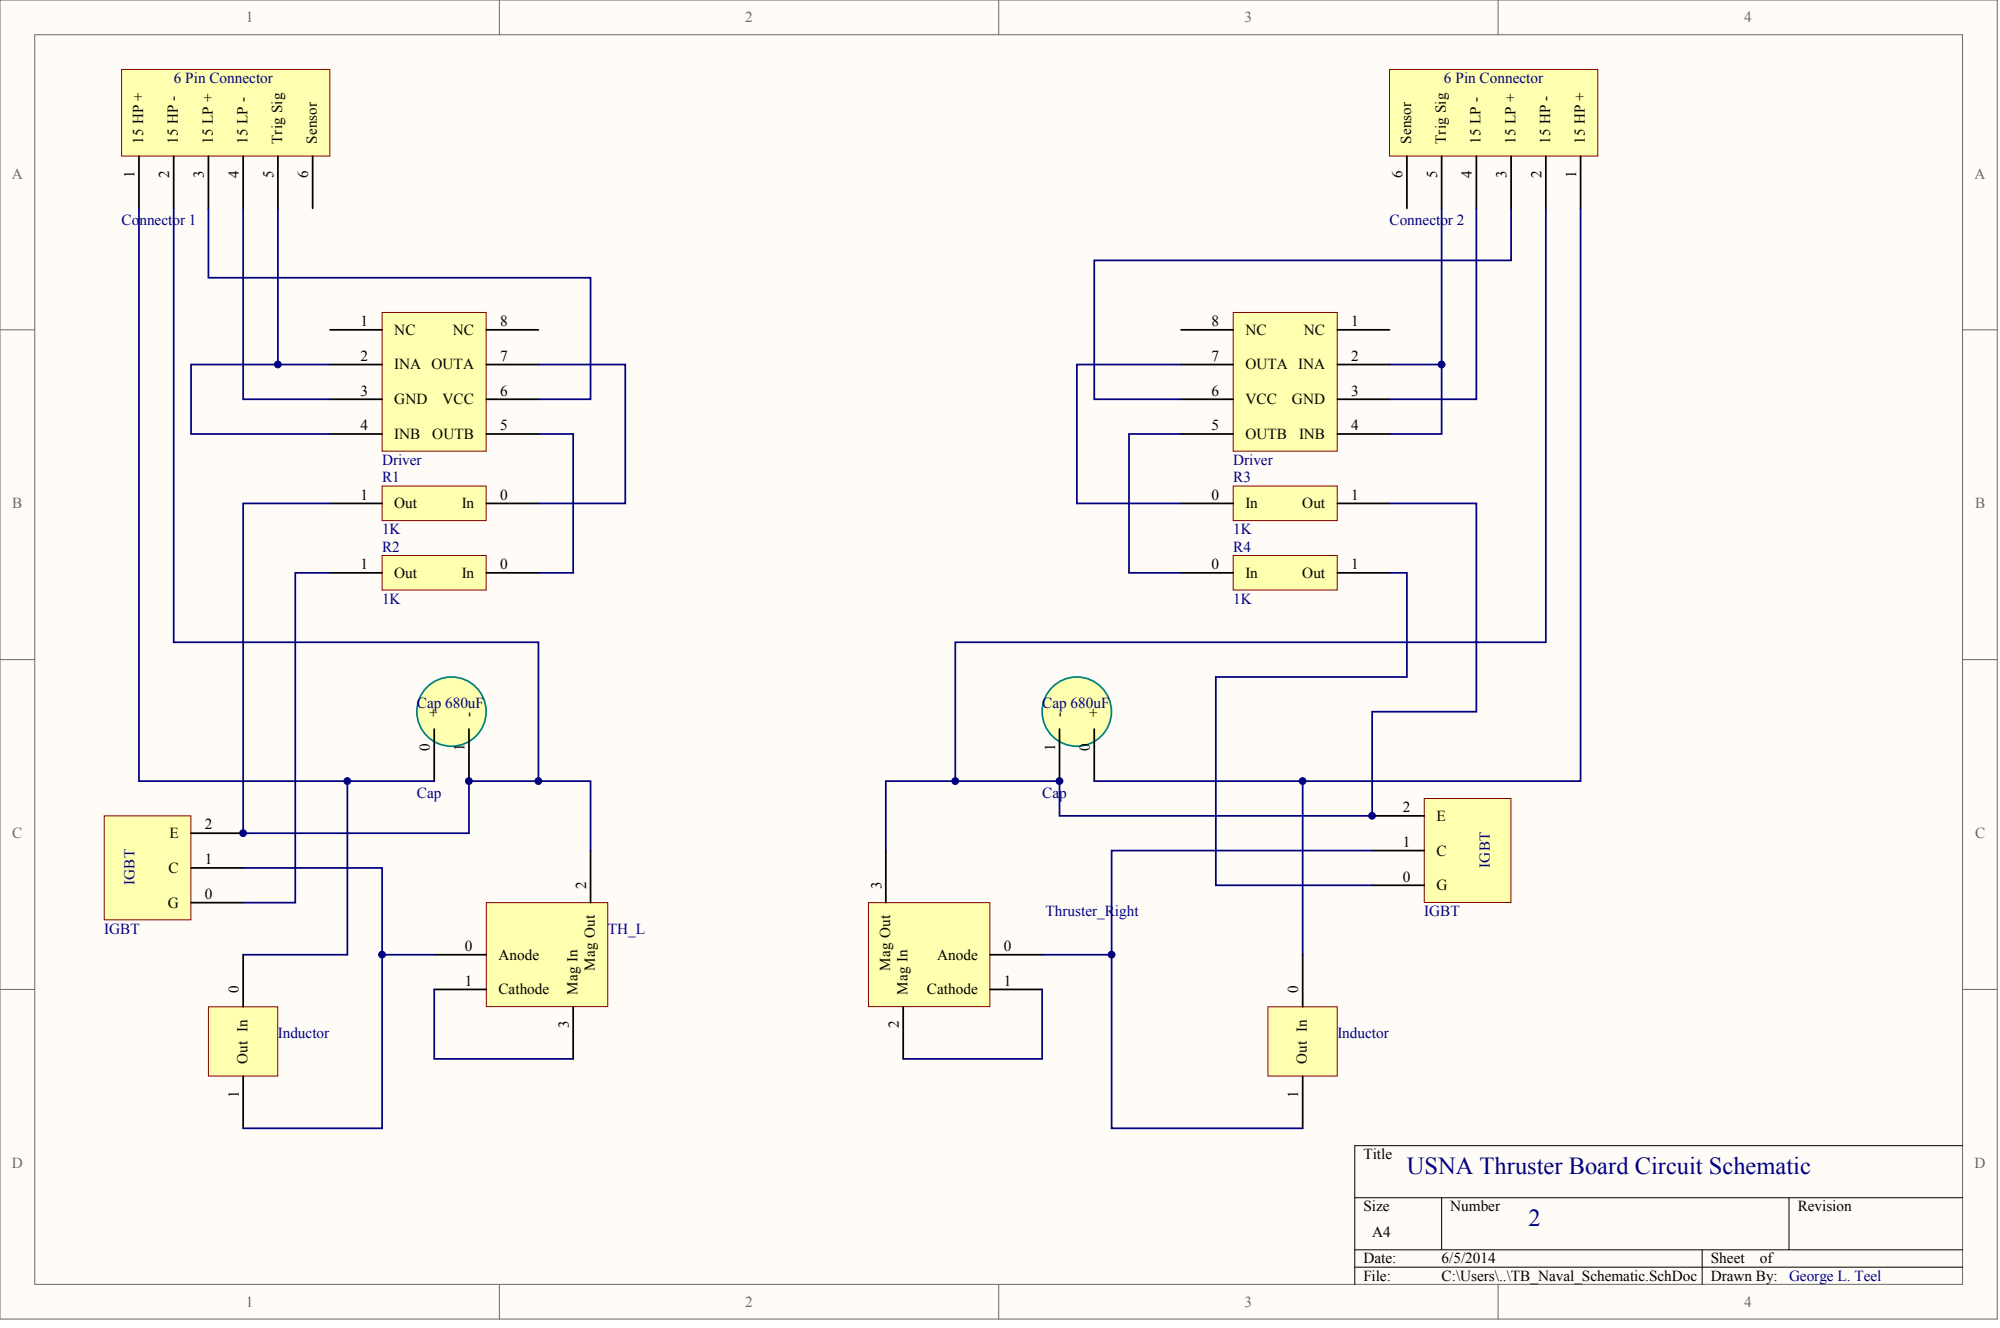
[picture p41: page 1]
Date:; Sheet of File:; C:\Users\..\TB_Naval_Schematic.SchDoc; Drawn By; Trig Sig 5; Sensor 6; 6 Pin Connector; Connector 1; Connector 2; 0 Out; Cap 680uF; In 0 Out 1; Mag Out 3; Mag In 2; George L. Teel

Cap 680uF

Mag Out 2 Mag In 3

Title
USNA Thruster Board Circuit Schematic 2

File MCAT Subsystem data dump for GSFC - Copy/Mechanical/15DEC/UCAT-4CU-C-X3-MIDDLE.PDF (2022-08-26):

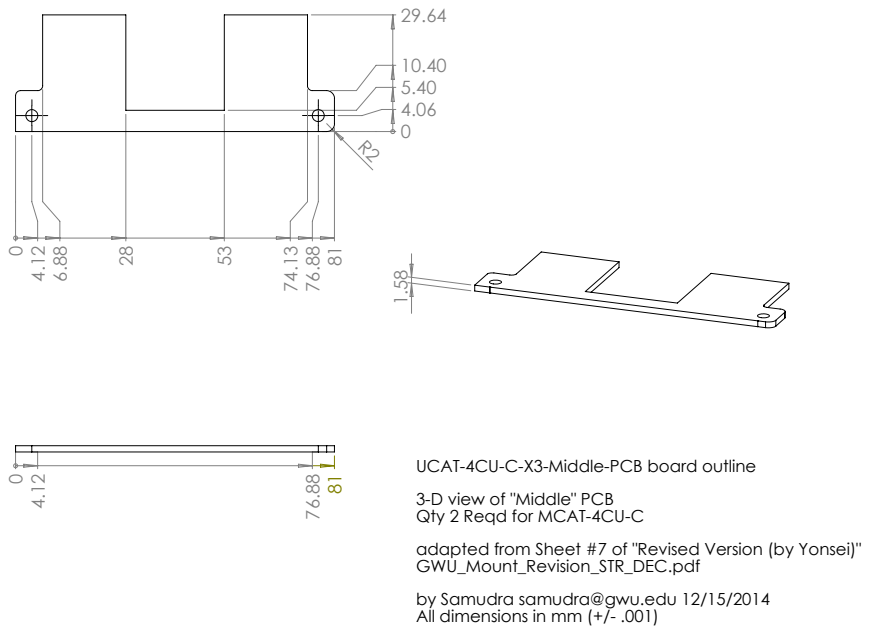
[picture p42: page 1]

UCAT-4CU-C-X3-Middle-PCB board outline
3-D view of "Middle" PCB
Qty 2 Reqd for MCAT-4CU-C
adapted from Sheet #7 of "Revised Version (by Yonsei)"
GWU_Mount_Revision_STR_DEC.pdf
by Samudra samudra@gwu.edu 12/15/2014
All dimensions in mm (+/- .001)

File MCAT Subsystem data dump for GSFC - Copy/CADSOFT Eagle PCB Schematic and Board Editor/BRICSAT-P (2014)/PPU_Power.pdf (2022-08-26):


Mag Out 2 Mag In 3

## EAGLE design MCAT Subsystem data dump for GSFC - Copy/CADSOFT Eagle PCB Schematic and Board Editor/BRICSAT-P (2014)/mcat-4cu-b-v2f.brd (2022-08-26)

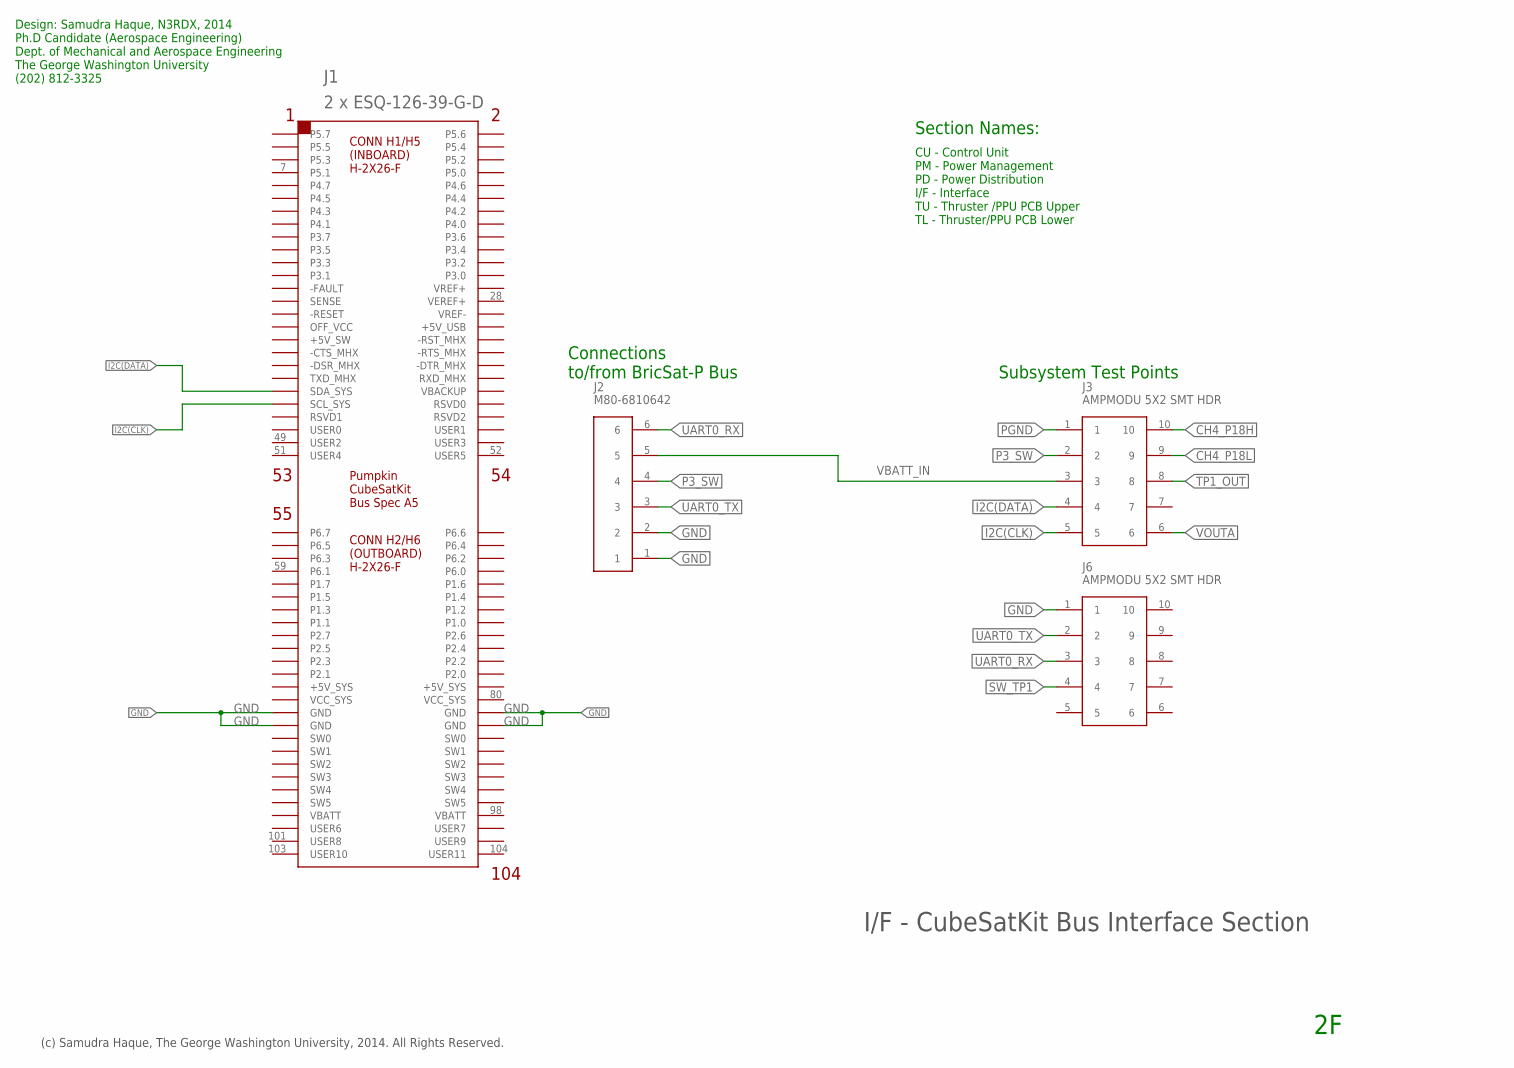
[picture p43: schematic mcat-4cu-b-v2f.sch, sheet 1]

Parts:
J1: 2 x ESQ-126-39-G-D; CSK-BUS-PKG
J2: M80-6810642; M80-68106
J3, J6: AMPMODU 5X2 SMT HDR; AMPMODU-SMT-PIN-HEADER-5X2

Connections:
CH4_P18H: J3.10; also elsewhere on the board
CH4_P18L: J3.9; also elsewhere on the board
GND: J1.81 (GND), J1.82 (GND), J1.83 (GND), J1.84 (GND), J2.1, J2.2, J6.1; also elsewhere on the board
I2C(CLK): J1.43 (SCL_SYS), J3.5; also elsewhere on the board
I2C(DATA): J1.41 (SDA_SYS), J3.4; also elsewhere on the board
P3_SW: J2.4, J3.2; also elsewhere on the board
PGND: J3.1; also elsewhere on the board
SW_TP1: J6.4; also elsewhere on the board
TP1_OUT: J3.8; also elsewhere on the board
UART0_RX: J2.6, J6.3; also elsewhere on the board
UART0_TX: J2.3, J6.2; also elsewhere on the board
VBATT_IN: J2.5, J3.3; also elsewhere on the board
VOUTA: J3.6; also elsewhere on the board

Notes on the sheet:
I/F - CubeSatKit Bus Interface Section
Subsystem Test Points
(c) Samudra Haque, The George Washington University, 2014. All Rights Reserved.
Connections to/from BricSat-P Bus
Design: Samudra Haque, N3RDX, 2014 Ph.D Candidate (Aerospace Engineering) Dept. of Mechanical and Aerospace Engineering The George Washington University (202) 812-3325
Section Names:
CU - Control Unit PM - Power Management PD - Power Distribution I/F - Interface TU - Thruster /PPU PCB Upper TL - Thruster/PPU PCB Lower

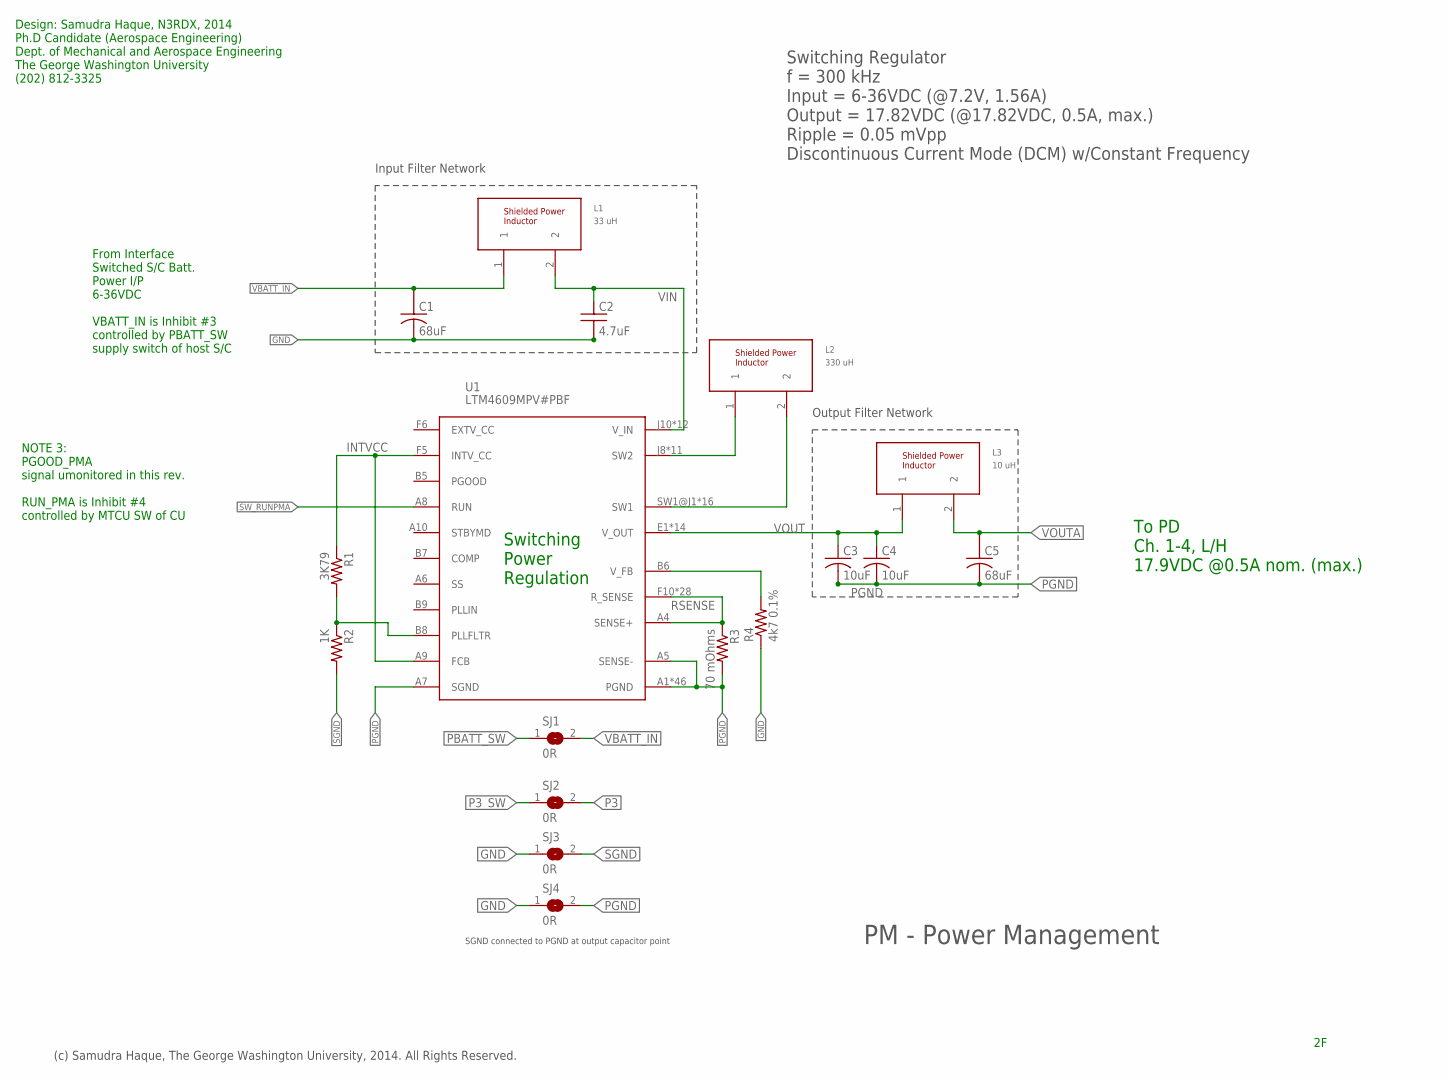
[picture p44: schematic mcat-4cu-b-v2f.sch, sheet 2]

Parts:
C1, C5: 68uF; OS-CON-SVPF-F12
C2: 4.7uF; MLCC-X7R-1210
C3, C4: 10uF; C1210K
L1: 33 uH; MSS1048
L2: 330 uH; MSS1048
L3: 10 uH; SERIES-POWER-INDUCTORS
R1: 3K79; R0805
R2: 1K; R0805
R3: 70 mOhms; R1206
R4: 4k7 0.1%; R0603
SJ1, SJ2, SJ3, SJ4: 0R; SJ
U1: LTM4609MPV#PBF; LGA-141-LTC-05-08-1840-B

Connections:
GND: C1.K1 (K), C2.2, R4.1, SJ3.1, SJ4.1; also elsewhere on the board
INTVCC: R1.1, U1.A9 (FCB), U1.F5 (INTV_CC)
P3: SJ2.2; also elsewhere on the board
P3_SW: SJ2.1; also elsewhere on the board
PBATT_SW: SJ1.1
PGND: C3.2, C4.2, C5.K1 (K), R3.2, SJ4.2, U1.A1 (PGND), U1.A2 (PGND), U1.A3 (PGND), U1.A5 (SENSE-), U1.A7 (SGND), U1.A11 (PGND), U1.A12 (PGND), U1.B1 (PGND), U1.B2 (PGND), U1.B3 (PGND), U1.B4 (PGND), U1.B10 (PGND), U1.B11 (PGND), U1.B12 (PGND), U1.C1 (PGND), U1.C2 (PGND), U1.C3 (PGND), U1.C4 (PGND), U1.C5 (PGND), U1.C6 (PGND), U1.C7 (PGND), U1.C8 (PGND), U1.C9 (PGND), U1.C10 (PGND), U1.C11 (PGND), U1.C12 (PGND), U1.D1 (PGND), U1.D2 (PGND), U1.D3 (PGND), U1.D4 (PGND), U1.D5 (PGND), U1.D6 (PGND), U1.D7 (PGND), U1.D8 (PGND), U1.D9 (PGND), U1.D10 (PGND), U1.D11 (PGND), U1.D12 (PGND), U1.E3 (PGND), U1.E4 (PGND), U1.E5 (PGND), U1.E6 (PGND), U1.E7 (PGND), U1.E8 (PGND), U1.E9 (PGND), U1.E10 (PGND), U1.E11 (PGND), U1.E12 (PGND); also elsewhere on the board
RSENSE: R3.1, U1.A4 (SENSE+), U1.F10 (R_SENSE), U1.F11 (R_SENSE), U1.F12 (R_SENSE), U1.G5 (R_SENSE), U1.G6 (R_SENSE), U1.G7 (R_SENSE), U1.G8 (R_SENSE), U1.G9 (R_SENSE), U1.G10 (R_SENSE), U1.G11 (R_SENSE), U1.G12 (R_SENSE), U1.H5 (R_SENSE), U1.H6 (R_SENSE), U1.H7 (R_SENSE), U1.H8 (R_SENSE), U1.H9 (R_SENSE), U1.H10 (R_SENSE), U1.H11 (R_SENSE), U1.H12 (R_SENSE), U1.J5 (R_SENSE), U1.J6 (R_SENSE), U1.J7 (R_SENSE), U1.K5 (R_SENSE), U1.K6 (R_SENSE), U1.L5 (R_SENSE), U1.L6 (R_SENSE), U1.M5 (R_SENSE), U1.M6 (R_SENSE)
SETFREQ: R1.2, R2.1, U1.B8 (PLLFLTR)
SGND: R2.2, SJ3.2; also elsewhere on the board
SW1: L2.2, U1.SW1@J1 (SW1), U1.SW1@J2 (SW1), U1.SW1@J3 (SW1), U1.SW1@J4 (SW1), U1.SW1@K1 (SW1), U1.SW1@K2 (SW1), U1.SW1@K3 (SW1), U1.SW1@K4 (SW1), U1.SW1@L1 (SW1), U1.SW1@L2 (SW1), U1.SW1@L3 (SW1), U1.SW1@L4 (SW1), U1.SW1@M1 (SW1), U1.SW1@M2 (SW1), U1.SW1@M3 (SW1), U1.SW1@M4 (SW1)
SW2: L2.1, U1.J8 (SW2), U1.J9 (SW2), U1.K7 (SW2), U1.K8 (SW2), U1.K9 (SW2), U1.L7 (SW2), U1.L8 (SW2), U1.L9 (SW2), U1.M7 (SW2), U1.M8 (SW2), U1.M9 (SW2)
SW_RUNPMA: U1.A8 (RUN); also elsewhere on the board
VBATT_IN: C1.A1 (A), L1.1, SJ1.2; also elsewhere on the board
VFB: R4.2, U1.B6 (V_FB)
VIN: C2.1, L1.2, U1.J10 (V_IN), U1.J11 (V_IN), U1.J12 (V_IN), U1.K10 (V_IN), U1.K11 (V_IN), U1.K12 (V_IN), U1.L10 (V_IN), U1.L11 (V_IN), U1.L12 (V_IN), U1.M10 (V_IN), U1.M11 (V_IN), U1.M12 (V_IN)
VOUT: C3.1, C4.1, L3.1, U1.E1 (V_OUT), U1.E2 (V_OUT), U1.F1 (V_OUT), U1.F2 (V_OUT), U1.F3 (V_OUT), U1.F4 (V_OUT), U1.G1 (V_OUT), U1.G2 (V_OUT), U1.G3 (V_OUT), U1.G4 (V_OUT), U1.H2 (V_OUT), U1.H3 (V_OUT), U1.H4 (V_OUT), U1.VOUT (V_OUT)
VOUTA: C5.A1 (A), L3.2; also elsewhere on the board

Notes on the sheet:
PM - Power Management
Input Filter Network
SGND connected to PGND at output capacitor point
Output Filter Network
Switching Regulator f = 300 kHz Input = 6-36VDC (@7.2V, 1.56A) Output = 17.82VDC (@17.82VDC, 0.5A, max.) Ripple = 0.05 mVpp Discontinuous Current Mode (DCM) w/Constant Frequency
(c) Samudra Haque, The George Washington University, 2014. All Rights Reserved.
NOTE 3: PGOOD_PMA signal umonitored in this rev. RUN_PMA is Inhibit #4 controlled by MTCU SW of CU
Switching Power Regulation
To PD Ch. 1-4, L/H 17.9VDC @0.5A nom. (max.)
From Interface Switched S/C Batt. Power I/P 6-36VDC VBATT_IN is Inhibit #3 controlled by PBATT_SW supply switch of host S/C
Design: Samudra Haque, N3RDX, 2014 Ph.D Candidate (Aerospace Engineering) Dept. of Mechanical and Aerospace Engineering The George Washington University (202) 812-3325

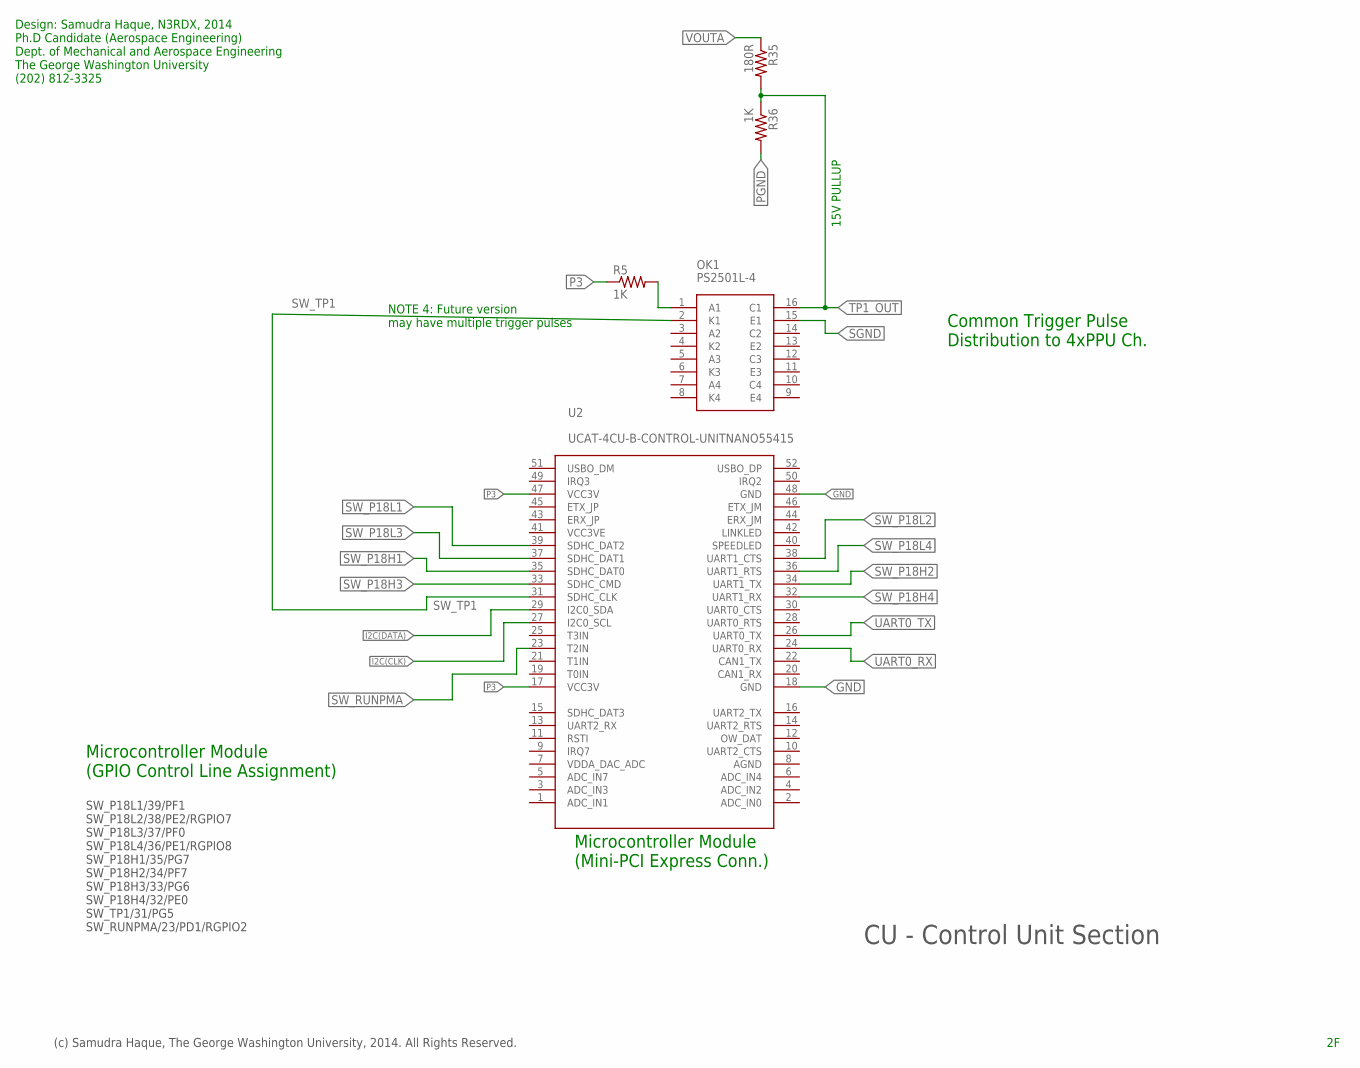
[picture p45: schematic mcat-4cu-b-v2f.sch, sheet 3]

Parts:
OK1: PS2501L-4
R5, R36: 1K; R0805
R35: 180R; R0805
U2: UCAT-4CU-B-CONTROL-UNITNANO55415; MOLEX-MINI-PCI-EXPRESS-8MM-52CKT

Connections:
GND: U2.18 (GND), U2.48 (GND); also elsewhere on the board
I2C(CLK): U2.27 (I2C0_SCL); also elsewhere on the board
I2C(DATA): U2.29 (I2C0_SDA); also elsewhere on the board
unnamed: OK1.1 (A1), R5.2
P3: R5.1, U2.17 (VCC3V), U2.47 (VCC3V); also elsewhere on the board
PGND: R36.2; also elsewhere on the board
SGND: OK1.15 (E1); also elsewhere on the board
SW_P18H1: U2.35 (SDHC_DAT0); also elsewhere on the board
SW_P18H2: U2.34 (UART1_TX); also elsewhere on the board
SW_P18H3: U2.33 (SDHC_CMD); also elsewhere on the board
SW_P18H4: U2.32 (UART1_RX); also elsewhere on the board
SW_P18L1: U2.39 (SDHC_DAT2); also elsewhere on the board
SW_P18L2: U2.38 (UART1_CTS); also elsewhere on the board
SW_P18L3: U2.37 (SDHC_DAT1); also elsewhere on the board
SW_P18L4: U2.36 (UART1_RTS); also elsewhere on the board
SW_RUNPMA: U2.23 (T2IN); also elsewhere on the board
SW_TP1: OK1.2 (K1), U2.31 (SDHC_CLK); also elsewhere on the board
TP1_OUT: OK1.16 (C1), R35.2, R36.1; also elsewhere on the board
UART0_RX: U2.24 (UART0_RX); also elsewhere on the board
UART0_TX: U2.26 (UART0_TX); also elsewhere on the board
VOUTA: R35.1; also elsewhere on the board

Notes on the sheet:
CU - Control Unit Section
SW_P18L1/39/PF1 SW_P18L2/38/PE2/RGPIO7 SW_P18L3/37/PF0 SW_P18L4/36/PE1/RGPIO8 SW_P18H1/35/PG7 SW_P18H2/34/PF7 SW_P18H3/33/PG6 SW_P18H4/32/PE0 SW_TP1/31/PG5 SW_RUNPMA/23/PD1/RGPIO2
(c) Samudra Haque, The George Washington University, 2014. All Rights Reserved.
Microcontroller Module (Mini-PCI Express Conn.)
Common Trigger Pulse Distribution to 4xPPU Ch.
NOTE 4: Future version may have multiple trigger pulses
Microcontroller Module (GPIO Control Line Assignment)
Design: Samudra Haque, N3RDX, 2014 Ph.D Candidate (Aerospace Engineering) Dept. of Mechanical and Aerospace Engineering The George Washington University (202) 812-3325
15V PULLUP

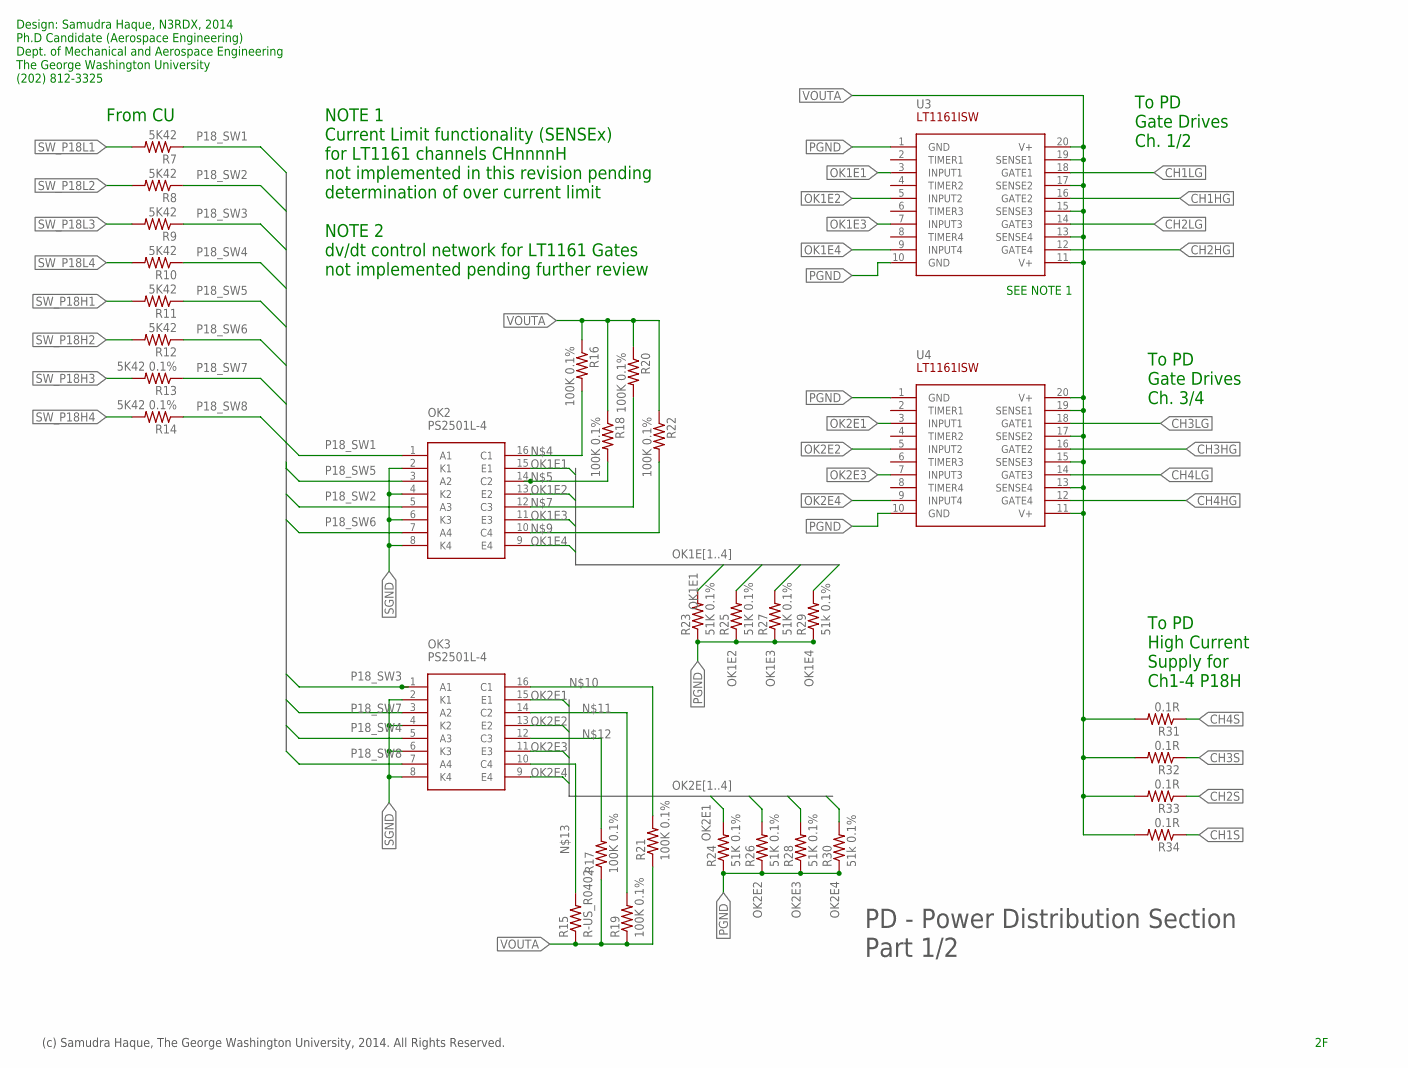
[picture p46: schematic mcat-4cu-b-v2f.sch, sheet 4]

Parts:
OK2, OK3: PS2501L-4
R7, R8, R9, R10, R11, R12: 5K42; R1206
R13, R14: 5K42 0.1%; R1206
R15: R-US_R0402; R0402
R16, R17, R18, R19, R20, R21, R22: 100K 0.1%; R0402
R23, R24, R25, R26, R27, R28: 51K 0.1%; R0603
R29, R30: 51k 0.1%; R0603
R31, R32, R33, R34: 0.1R; R0402
U3, U4: LT1161ISW; 20-LEAD-PLASTIC-SO

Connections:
CH1HG: U3.16 (GATE2); also elsewhere on the board
CH1LG: U3.18 (GATE1); also elsewhere on the board
CH1S: R34.1; also elsewhere on the board
CH2HG: U3.12 (GATE4); also elsewhere on the board
CH2LG: U3.14 (GATE3); also elsewhere on the board
CH2S: R33.1; also elsewhere on the board
CH3HG: U4.16 (GATE2); also elsewhere on the board
CH3LG: U4.18 (GATE1); also elsewhere on the board
CH3S: R32.1; also elsewhere on the board
CH4HG: U4.12 (GATE4); also elsewhere on the board
CH4LG: U4.14 (GATE3); also elsewhere on the board
CH4S: R31.1; also elsewhere on the board
unnamed: OK2.16 (C1), R16.2
unnamed: OK2.14 (C2), R18.2
unnamed: OK2.12 (C3), R20.2
unnamed: OK2.10 (C4), R22.2
unnamed: OK3.16 (C1), R21.2
unnamed: OK3.14 (C2), R19.2
unnamed: OK3.12 (C3), R17.2
unnamed: OK3.10 (C4), R15.2
OK1E1: OK2.15 (E1), R23.2, U3.3 (INPUT1)
OK1E2: OK2.13 (E2), R25.2, U3.5 (INPUT2)
OK1E3: OK2.11 (E3), R27.2, U3.7 (INPUT3)
OK1E4: OK2.9 (E4), R29.2, U3.9 (INPUT4)
OK2E1: OK3.15 (E1), R24.2, U4.3 (INPUT1)
OK2E2: OK3.13 (E2), R26.2, U4.5 (INPUT2)
OK2E3: OK3.11 (E3), R28.2, U4.7 (INPUT3)
OK2E4: OK3.9 (E4), R30.2, U4.9 (INPUT4)
P18_SW1: OK2.1 (A1), R7.1
P18_SW2: OK2.5 (A3), R8.1
P18_SW3: OK3.1 (A1), R9.1
P18_SW4: OK3.5 (A3), R10.1
P18_SW5: OK2.3 (A2), R11.1
P18_SW6: OK2.7 (A4), R12.1
P18_SW7: OK3.3 (A2), R13.1
P18_SW8: OK3.7 (A4), R14.1
PGND: R23.1, R24.1, R25.1, R26.1, R27.1, R28.1, R29.1, R30.1, U3.1 (GND), U3.10 (GND), U4.1 (GND), U4.10 (GND); also elsewhere on the board
SGND: OK2.2 (K1), OK2.4 (K2), OK2.6 (K3), OK2.8 (K4), OK3.2 (K1), OK3.4 (K2), OK3.6 (K3), OK3.8 (K4); also elsewhere on the board
SW_P18H1: R11.2; also elsewhere on the board
SW_P18H2: R12.2; also elsewhere on the board
SW_P18H3: R13.2; also elsewhere on the board
SW_P18H4: R14.2; also elsewhere on the board
SW_P18L1: R7.2; also elsewhere on the board
SW_P18L2: R8.2; also elsewhere on the board
SW_P18L3: R9.2; also elsewhere on the board
SW_P18L4: R10.2; also elsewhere on the board
VOUTA: R15.1, R16.1, R17.1, R18.1, R19.1, R20.1, R21.1, R22.1, R31.2, R32.2, R33.2, R34.2, U3.11 (V+), U3.13 (SENSE4), U3.15 (SENSE3), U3.17 (SENSE2), U3.19 (SENSE1), U3.20 (V+), U4.11 (V+), U4.13 (SENSE4), U4.15 (SENSE3), U4.17 (SENSE2), U4.19 (SENSE1), U4.20 (V+); also elsewhere on the board

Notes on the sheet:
PD - Power Distribution Section Part 1/2
NOTE 1 Current Limit functionality (SENSEx) for LT1161 channels CHnnnnH not implemented in this revision pending determination of over current limit NOTE 2 dv/dt control network for LT1161 Gates not implemented pending further review
SEE NOTE 1
(c) Samudra Haque, The George Washington University, 2014. All Rights Reserved.
From CU
To PD Gate Drives Ch. 1/2
To PD High Current Supply for Ch1-4 P18H
To PD Gate Drives Ch. 3/4
Design: Samudra Haque, N3RDX, 2014 Ph.D Candidate (Aerospace Engineering) Dept. of Mechanical and Aerospace Engineering The George Washington University (202) 812-3325

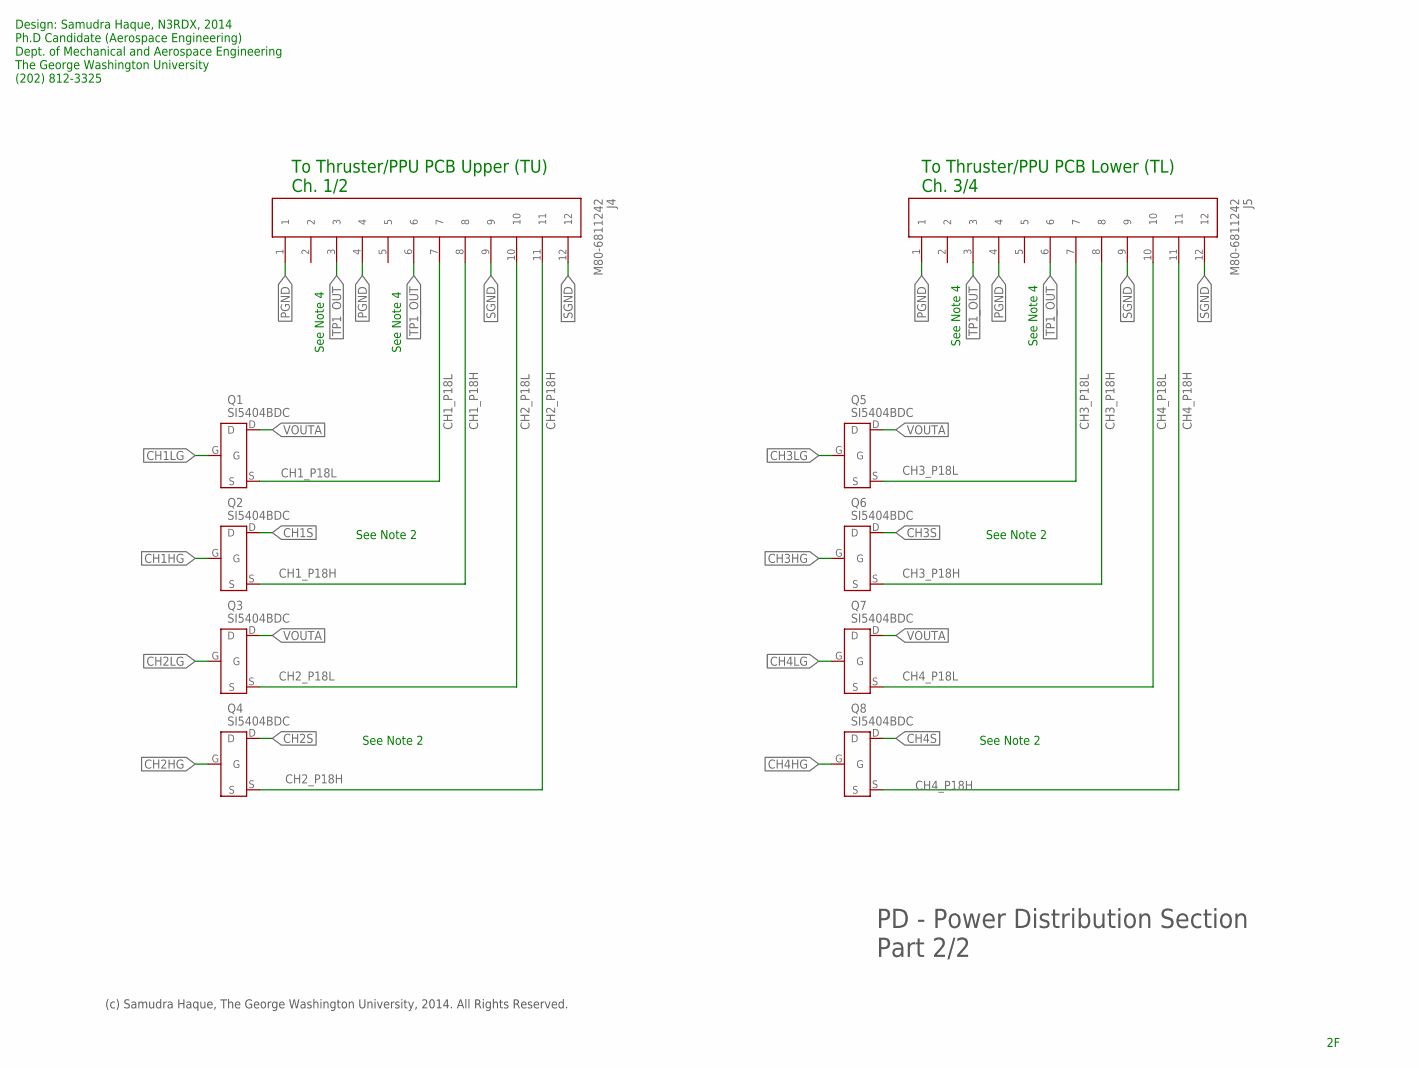
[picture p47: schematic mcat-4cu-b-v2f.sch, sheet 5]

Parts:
J4, J5: M80-6811242; M80-68112
Q1, Q2, Q3, Q4, Q5, Q6, Q7, Q8: SI5404BDC; 1206-8-CHIPFET

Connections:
CH1HG: Q2.G; also elsewhere on the board
CH1LG: Q1.G; also elsewhere on the board
CH1S: Q2.D; also elsewhere on the board
CH1_P18H: J4.8, Q2.S
CH1_P18L: J4.7, Q1.S
CH2HG: Q4.G; also elsewhere on the board
CH2LG: Q3.G; also elsewhere on the board
CH2S: Q4.D; also elsewhere on the board
CH2_P18H: J4.11, Q4.S
CH2_P18L: J4.10, Q3.S
CH3HG: Q6.G; also elsewhere on the board
CH3LG: Q5.G; also elsewhere on the board
CH3S: Q6.D; also elsewhere on the board
CH3_P18H: J5.8, Q6.S
CH3_P18L: J5.7, Q5.S
CH4HG: Q8.G; also elsewhere on the board
CH4LG: Q7.G; also elsewhere on the board
CH4S: Q8.D; also elsewhere on the board
CH4_P18H: J5.11, Q8.S; also elsewhere on the board
CH4_P18L: J5.10, Q7.S; also elsewhere on the board
PGND: J4.1, J4.4, J5.1, J5.4; also elsewhere on the board
SGND: J4.9, J4.12, J5.9, J5.12; also elsewhere on the board
TP1_OUT: J4.3, J4.6, J5.3, J5.6; also elsewhere on the board
VOUTA: Q1.D, Q3.D, Q5.D, Q7.D; also elsewhere on the board

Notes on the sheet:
PD - Power Distribution Section Part 2/2
(c) Samudra Haque, The George Washington University, 2014. All Rights Reserved.
See Note 2
To Thruster/PPU PCB Upper (TU) Ch. 1/2
To Thruster/PPU PCB Lower (TL) Ch. 3/4
See Note 4
Design: Samudra Haque, N3RDX, 2014 Ph.D Candidate (Aerospace Engineering) Dept. of Mechanical and Aerospace Engineering The George Washington University (202) 812-3325

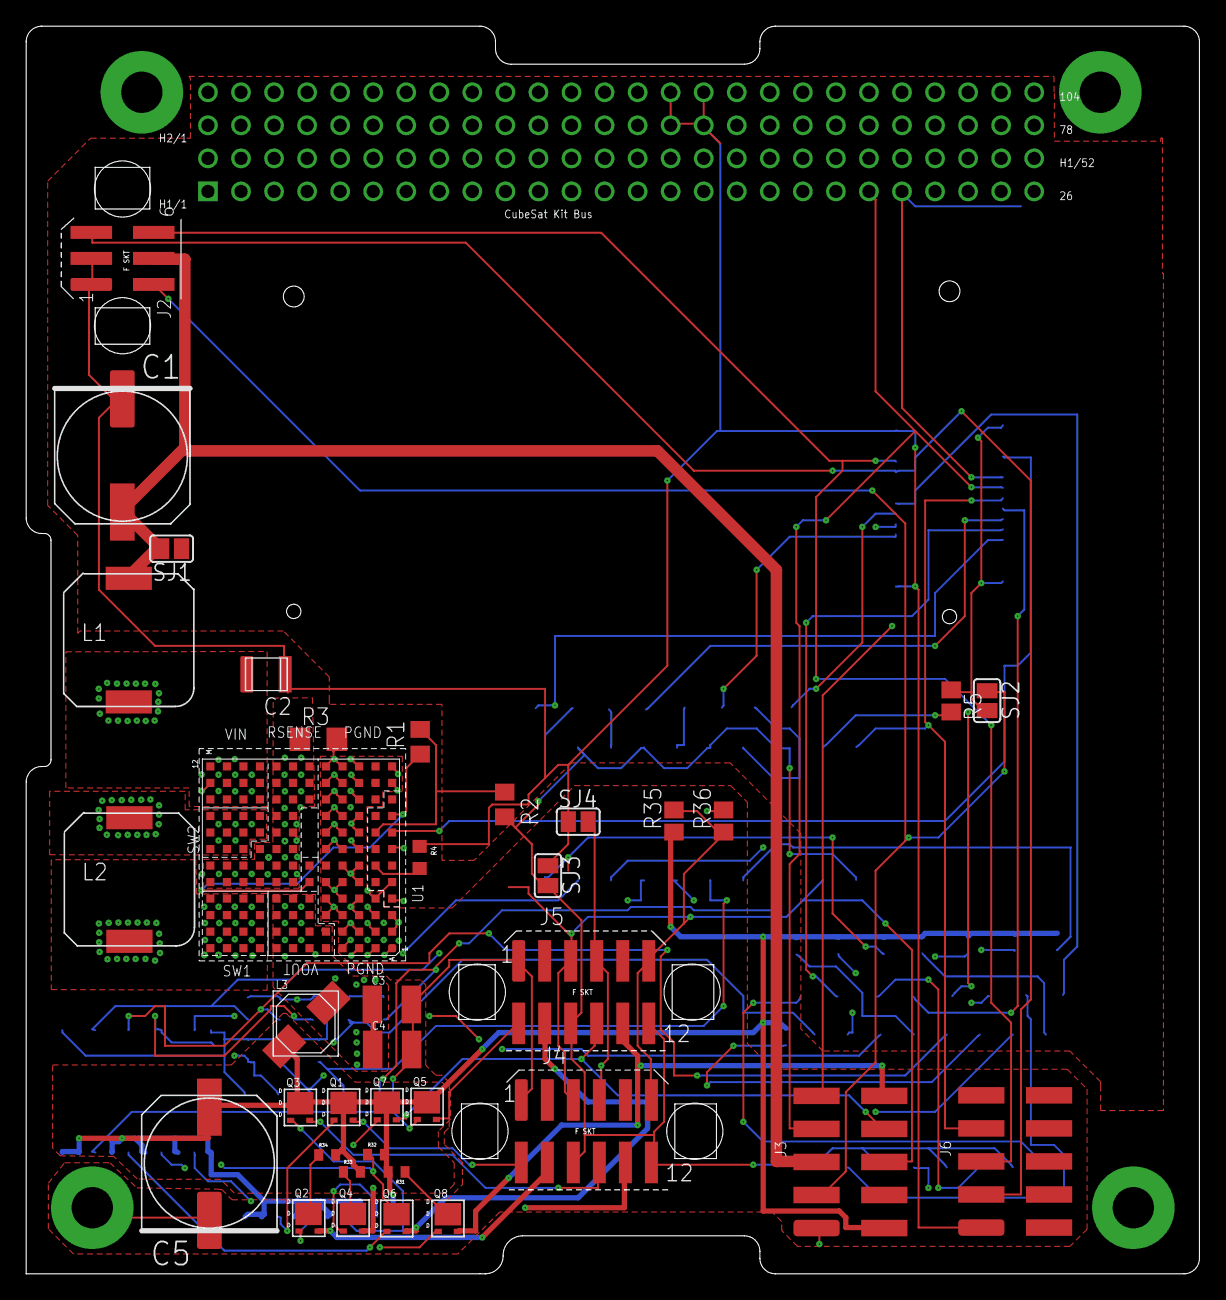
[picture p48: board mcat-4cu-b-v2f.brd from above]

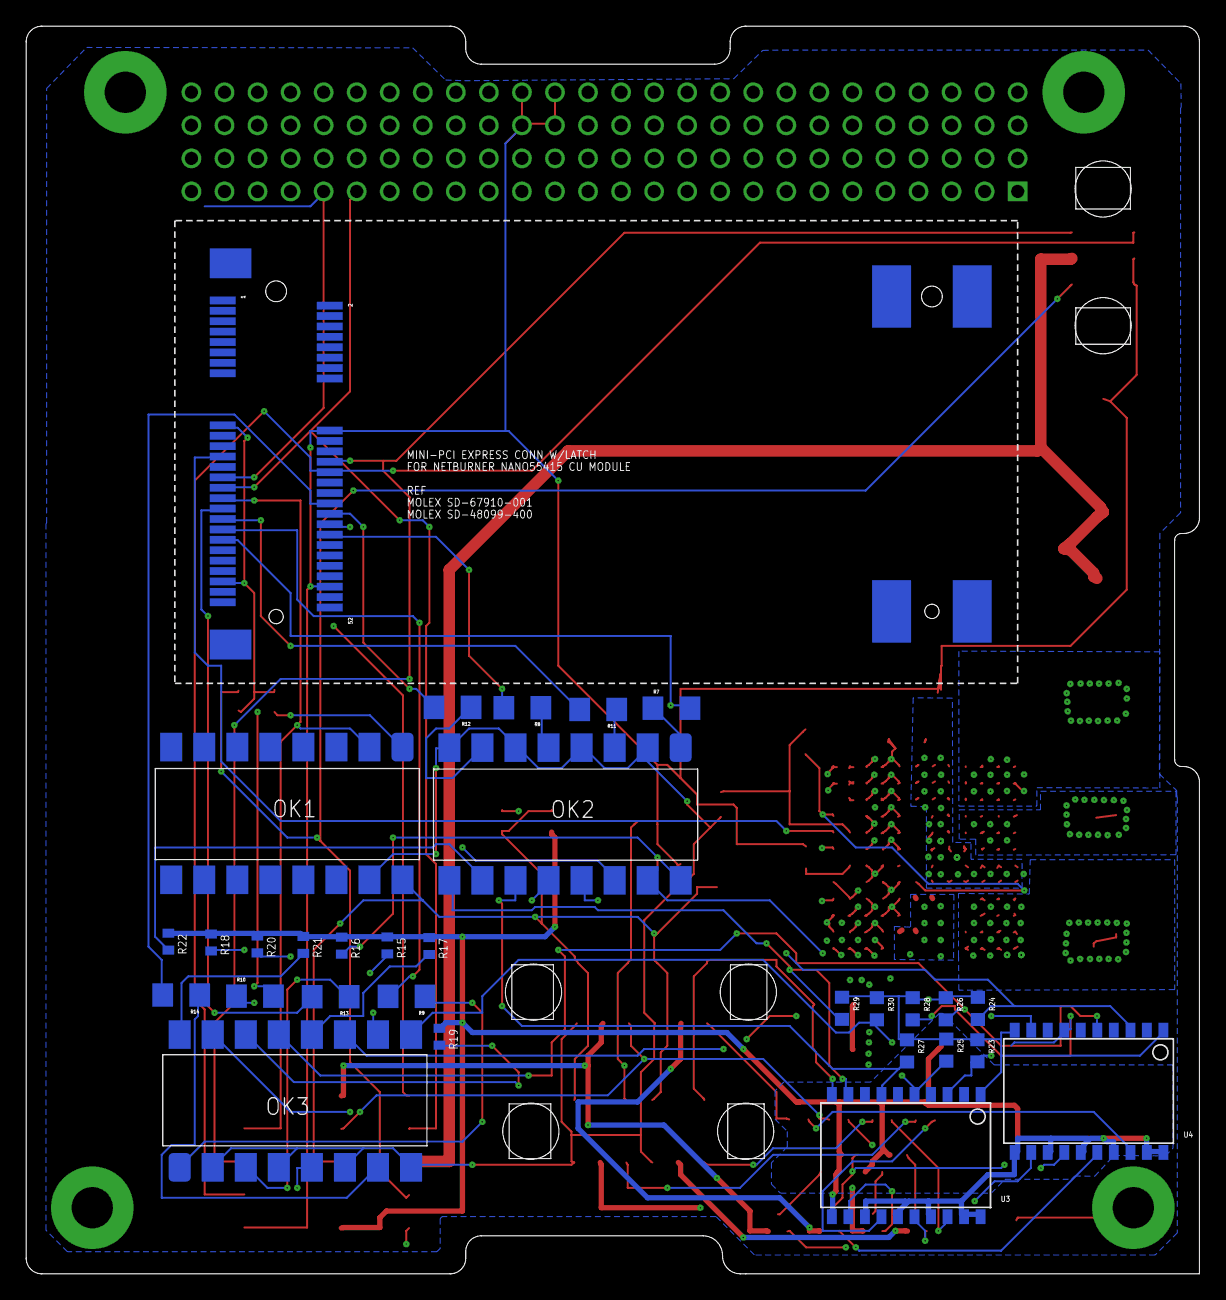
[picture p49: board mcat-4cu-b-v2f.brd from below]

Board: 4 copper layers, 90.2 x 95.9 mm, 68 parts (30 on the bottom side), 75 nets.

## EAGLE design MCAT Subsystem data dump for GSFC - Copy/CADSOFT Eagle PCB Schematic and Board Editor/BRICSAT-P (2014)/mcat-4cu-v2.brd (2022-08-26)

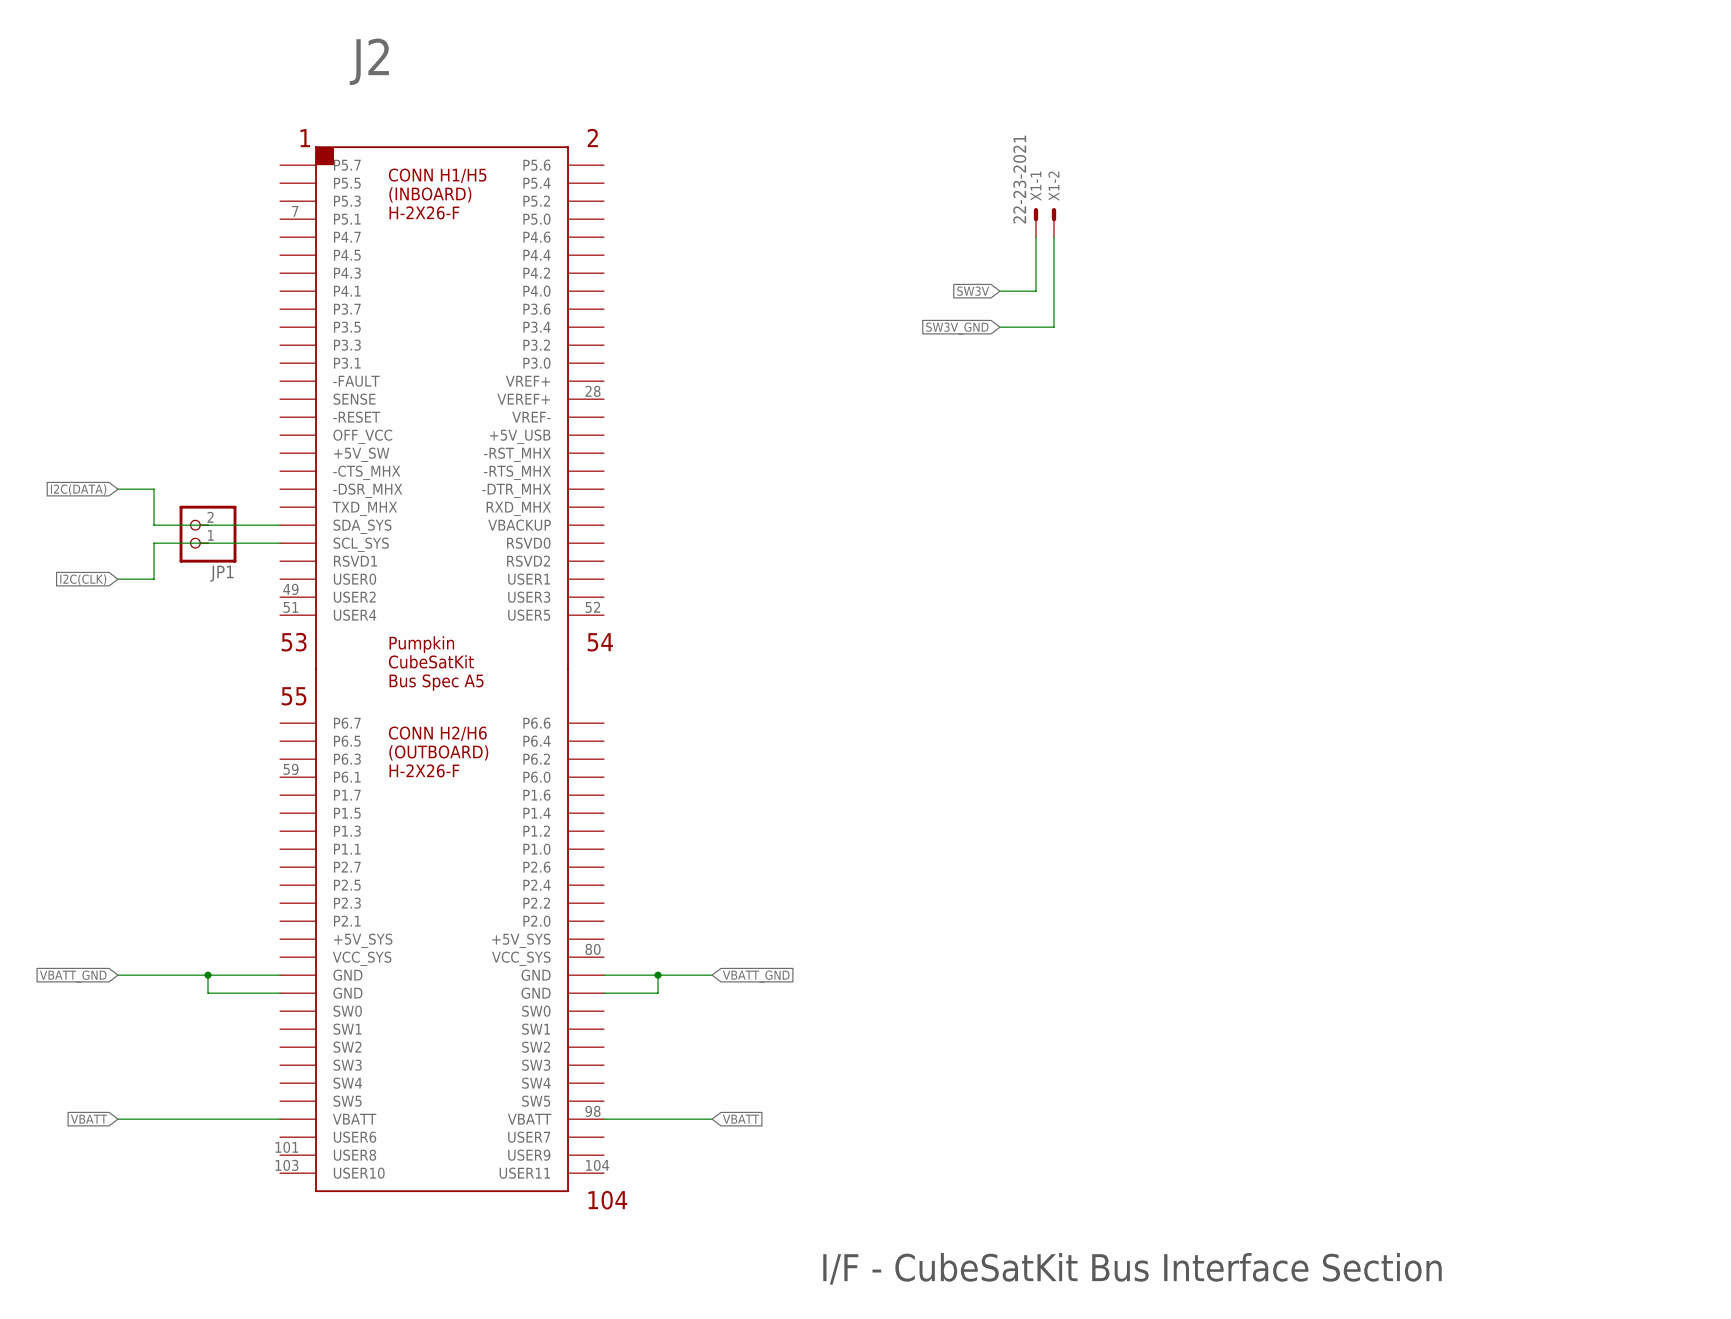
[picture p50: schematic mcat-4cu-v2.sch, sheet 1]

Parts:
J2: CSK-BUS-CONN2X2X26; CSK-BUS-PKG
JP1: PINHD-1X2; 1X02
X1: 22-23-2021

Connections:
I2C(CLK): J2.43 (SCL_SYS), JP1.1; also elsewhere on the board
I2C(DATA): J2.41 (SDA_SYS), JP1.2; also elsewhere on the board
unnamed: J2.82 (GND), J2.84 (GND)
SW3V: X1.1; also elsewhere on the board
SW3V_GND: X1.2; also elsewhere on the board
VBATT: J2.97 (VBATT), J2.98 (VBATT); also elsewhere on the board
VBATT_GND: J2.81 (GND), J2.83 (GND); also elsewhere on the board

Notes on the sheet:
I/F - CubeSatKit Bus Interface Section

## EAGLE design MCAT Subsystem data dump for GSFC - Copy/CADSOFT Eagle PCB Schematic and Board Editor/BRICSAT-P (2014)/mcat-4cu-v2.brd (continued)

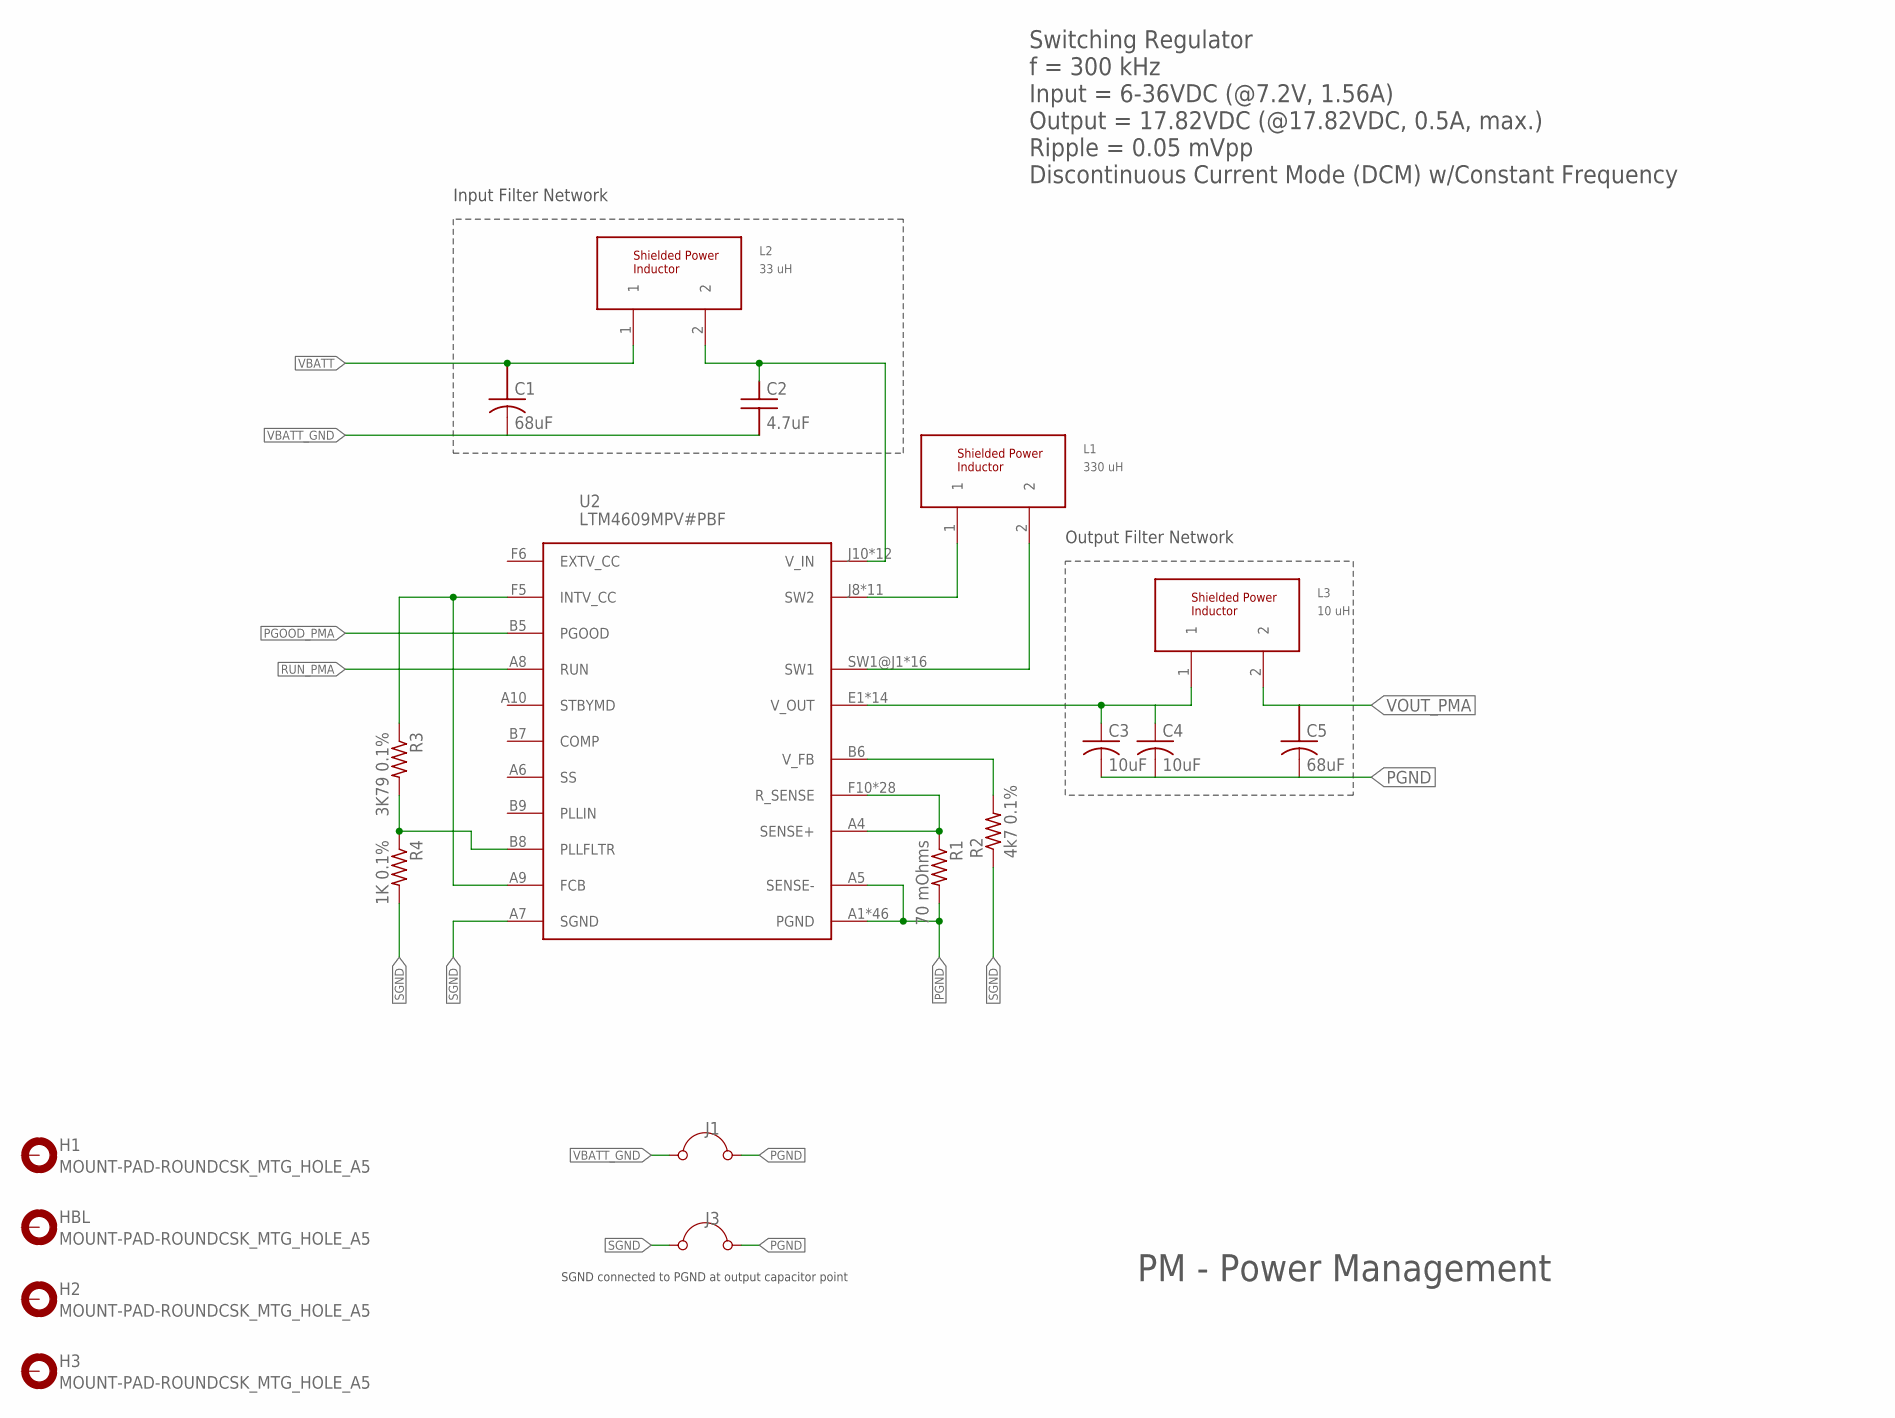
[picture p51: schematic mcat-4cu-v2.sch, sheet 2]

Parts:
C1, C5: 68uF; OS-CON-SVPF-F12
C2: 4.7uF; MLCC-X7R-1210
C3, C4: 10uF; C1210K
H1, H2, H3: MOUNT-PAD-ROUNDCSK_MTG_HOLE_A5; CSK_MOUNTING_HOLE
HBL: MOUNT-PAD-ROUNDCSK_MTG_HOLE_A5; CSK_MOUNTING_HOLE
J1, J3: JUMPER; 05
L1: 330 uH; MSS1048
L2: 33 uH; MSS1048
L3: 10 uH; SERIES-POWER-INDUCTORS
R1: 70 mOhms; R1206
R2: 4k7 0.1%; R0603
R3: 3K79 0.1%; R0805
R4: 1K 0.1%; R0805
U2: LTM4609MPV#PBF; LGA-141-LTC-05-08-1840-B

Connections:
INTVCC_OUT: R3.1, U2.A9 (FCB), U2.F5 (INTV_CC)
unnamed: R1.1, U2.A4 (SENSE+), U2.F10 (R_SENSE), U2.F11 (R_SENSE), U2.F12 (R_SENSE), U2.G5 (R_SENSE), U2.G6 (R_SENSE), U2.G7 (R_SENSE), U2.G8 (R_SENSE), U2.G9 (R_SENSE), U2.G10 (R_SENSE), U2.G11 (R_SENSE), U2.G12 (R_SENSE), U2.H5 (R_SENSE), U2.H6 (R_SENSE), U2.H7 (R_SENSE), U2.H8 (R_SENSE), U2.H9 (R_SENSE), U2.H10 (R_SENSE), U2.H11 (R_SENSE), U2.H12 (R_SENSE), U2.J5 (R_SENSE), U2.J6 (R_SENSE), U2.J7 (R_SENSE), U2.K5 (R_SENSE), U2.K6 (R_SENSE), U2.L5 (R_SENSE), U2.L6 (R_SENSE), U2.M5 (R_SENSE), U2.M6 (R_SENSE)
unnamed: R2.2, U2.B6 (V_FB)
PGND: C3.2, C4.2, C5.K1 (K), J1.2 (-), J3.2 (-), R1.2, U2.A1 (PGND), U2.A2 (PGND), U2.A3 (PGND), U2.A5 (SENSE-), U2.A11 (PGND), U2.A12 (PGND), U2.B1 (PGND), U2.B2 (PGND), U2.B3 (PGND), U2.B4 (PGND), U2.B10 (PGND), U2.B11 (PGND), U2.B12 (PGND), U2.C1 (PGND), U2.C2 (PGND), U2.C3 (PGND), U2.C4 (PGND), U2.C5 (PGND), U2.C6 (PGND), U2.C7 (PGND), U2.C8 (PGND), U2.C9 (PGND), U2.C10 (PGND), U2.C11 (PGND), U2.C12 (PGND), U2.D1 (PGND), U2.D2 (PGND), U2.D3 (PGND), U2.D4 (PGND), U2.D5 (PGND), U2.D6 (PGND), U2.D7 (PGND), U2.D8 (PGND), U2.D9 (PGND), U2.D10 (PGND), U2.D11 (PGND), U2.D12 (PGND), U2.E3 (PGND), U2.E4 (PGND), U2.E5 (PGND), U2.E6 (PGND), U2.E7 (PGND), U2.E8 (PGND), U2.E9 (PGND), U2.E10 (PGND), U2.E11 (PGND), U2.E12 (PGND)
PGOOD_PMA: U2.B5 (PGOOD)
RUN_PMA: U2.A8 (RUN)
SETFREQ: R3.2, R4.1, U2.B8 (PLLFLTR)
SGND: J3.1 (+), R2.1, R4.2, U2.A7 (SGND); also elsewhere on the board
SW1: L1.2, U2.SW1@J1 (SW1), U2.SW1@J2 (SW1), U2.SW1@J3 (SW1), U2.SW1@J4 (SW1), U2.SW1@K1 (SW1), U2.SW1@K2 (SW1), U2.SW1@K3 (SW1), U2.SW1@K4 (SW1), U2.SW1@L1 (SW1), U2.SW1@L2 (SW1), U2.SW1@L3 (SW1), U2.SW1@L4 (SW1), U2.SW1@M1 (SW1), U2.SW1@M2 (SW1), U2.SW1@M3 (SW1), U2.SW1@M4 (SW1)
SW2: L1.1, U2.J8 (SW2), U2.J9 (SW2), U2.K7 (SW2), U2.K8 (SW2), U2.K9 (SW2), U2.L7 (SW2), U2.L8 (SW2), U2.L9 (SW2), U2.M7 (SW2), U2.M8 (SW2), U2.M9 (SW2)
VBATT: C1.A1 (A), L2.1; also elsewhere on the board
VBATT_GND: C1.K1 (K), C2.2, J1.1 (+); also elsewhere on the board
VIN_PMA: C2.1, L2.2, U2.J10 (V_IN), U2.J11 (V_IN), U2.J12 (V_IN), U2.K10 (V_IN), U2.K11 (V_IN), U2.K12 (V_IN), U2.L10 (V_IN), U2.L11 (V_IN), U2.L12 (V_IN), U2.M10 (V_IN), U2.M11 (V_IN), U2.M12 (V_IN)
VOUTA: C3.1, C4.1, L3.1, U2.E1 (V_OUT), U2.E2 (V_OUT), U2.F1 (V_OUT), U2.F2 (V_OUT), U2.F3 (V_OUT), U2.F4 (V_OUT), U2.G1 (V_OUT), U2.G2 (V_OUT), U2.G3 (V_OUT), U2.G4 (V_OUT), U2.H2 (V_OUT), U2.H3 (V_OUT), U2.H4 (V_OUT), U2.VOUT (V_OUT)
VOUT_PMA: C5.A1 (A), L3.2

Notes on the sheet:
PM - Power Management
Input Filter Network
SGND connected to PGND at output capacitor point
Output Filter Network
Switching Regulator f = 300 kHz Input = 6-36VDC (@7.2V, 1.56A) Output = 17.82VDC (@17.82VDC, 0.5A, max.) Ripple = 0.05 mVpp Discontinuous Current Mode (DCM) w/Constant Frequency

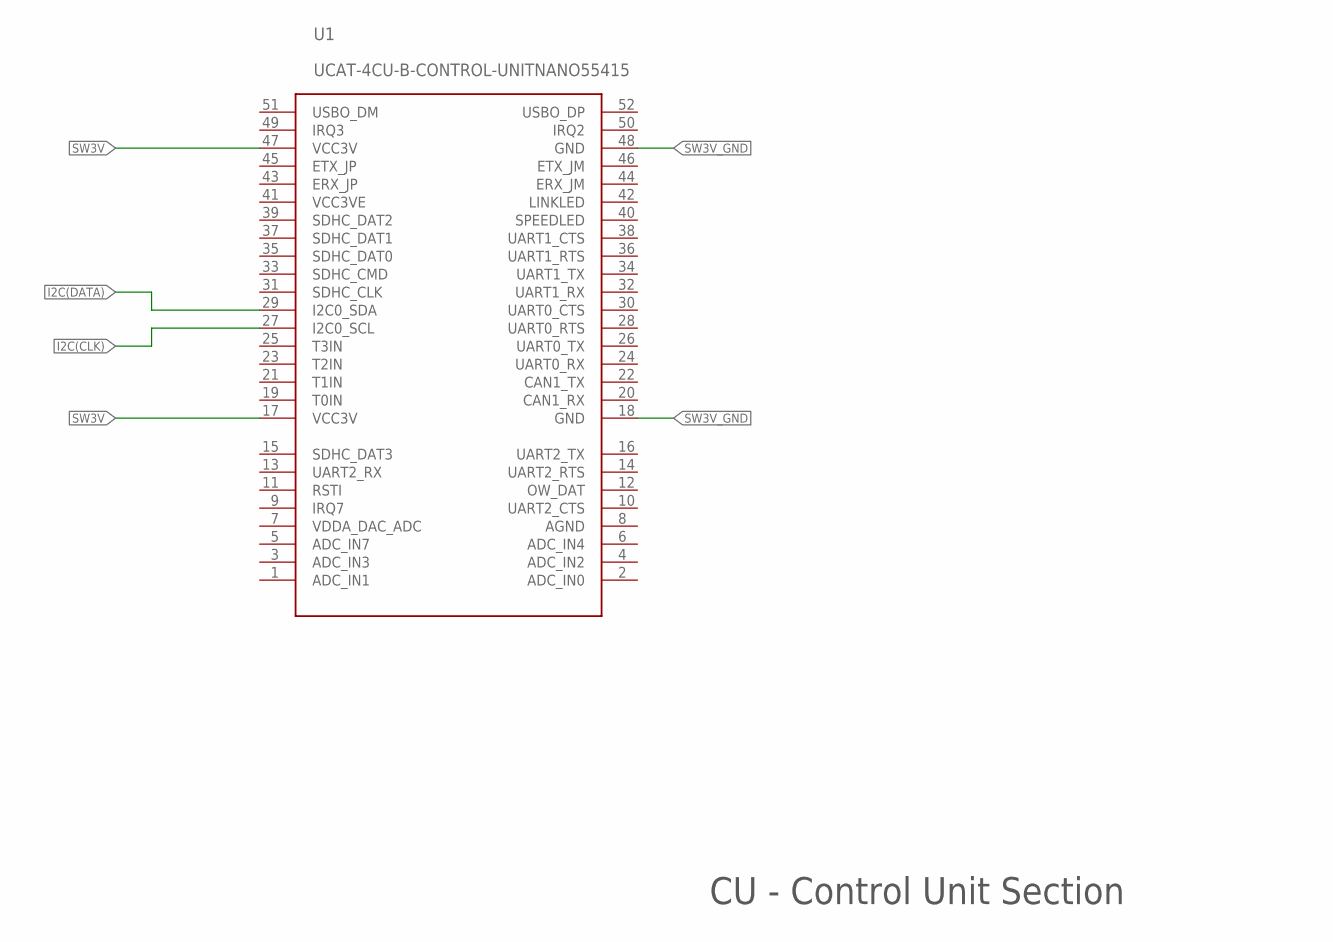
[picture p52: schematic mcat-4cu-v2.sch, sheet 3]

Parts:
U1: UCAT-4CU-B-CONTROL-UNITNANO55415; MOLEX-MINI-PCI-EXPRESS-8MM-52CKT

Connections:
I2C(CLK): U1.27 (I2C0_SCL); also elsewhere on the board
I2C(DATA): U1.29 (I2C0_SDA); also elsewhere on the board
SW3V: U1.17 (VCC3V), U1.47 (VCC3V); also elsewhere on the board
SW3V_GND: U1.48 (GND); also elsewhere on the board

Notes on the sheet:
CU - Control Unit Section

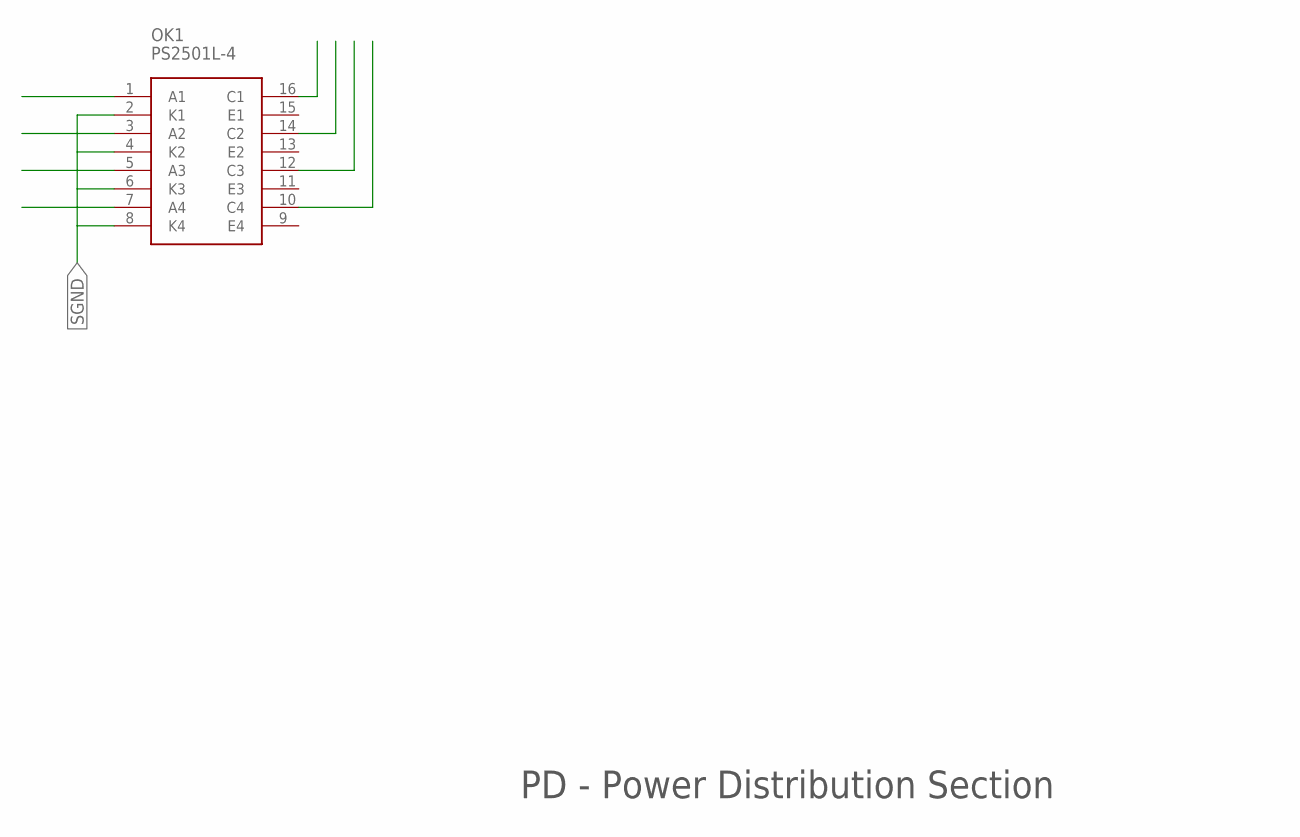
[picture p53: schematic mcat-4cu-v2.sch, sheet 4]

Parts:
OK1: PS2501L-4

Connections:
SGND: OK1.2 (K1), OK1.4 (K2), OK1.6 (K3), OK1.8 (K4); also elsewhere on the board

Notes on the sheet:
PD - Power Distribution Section

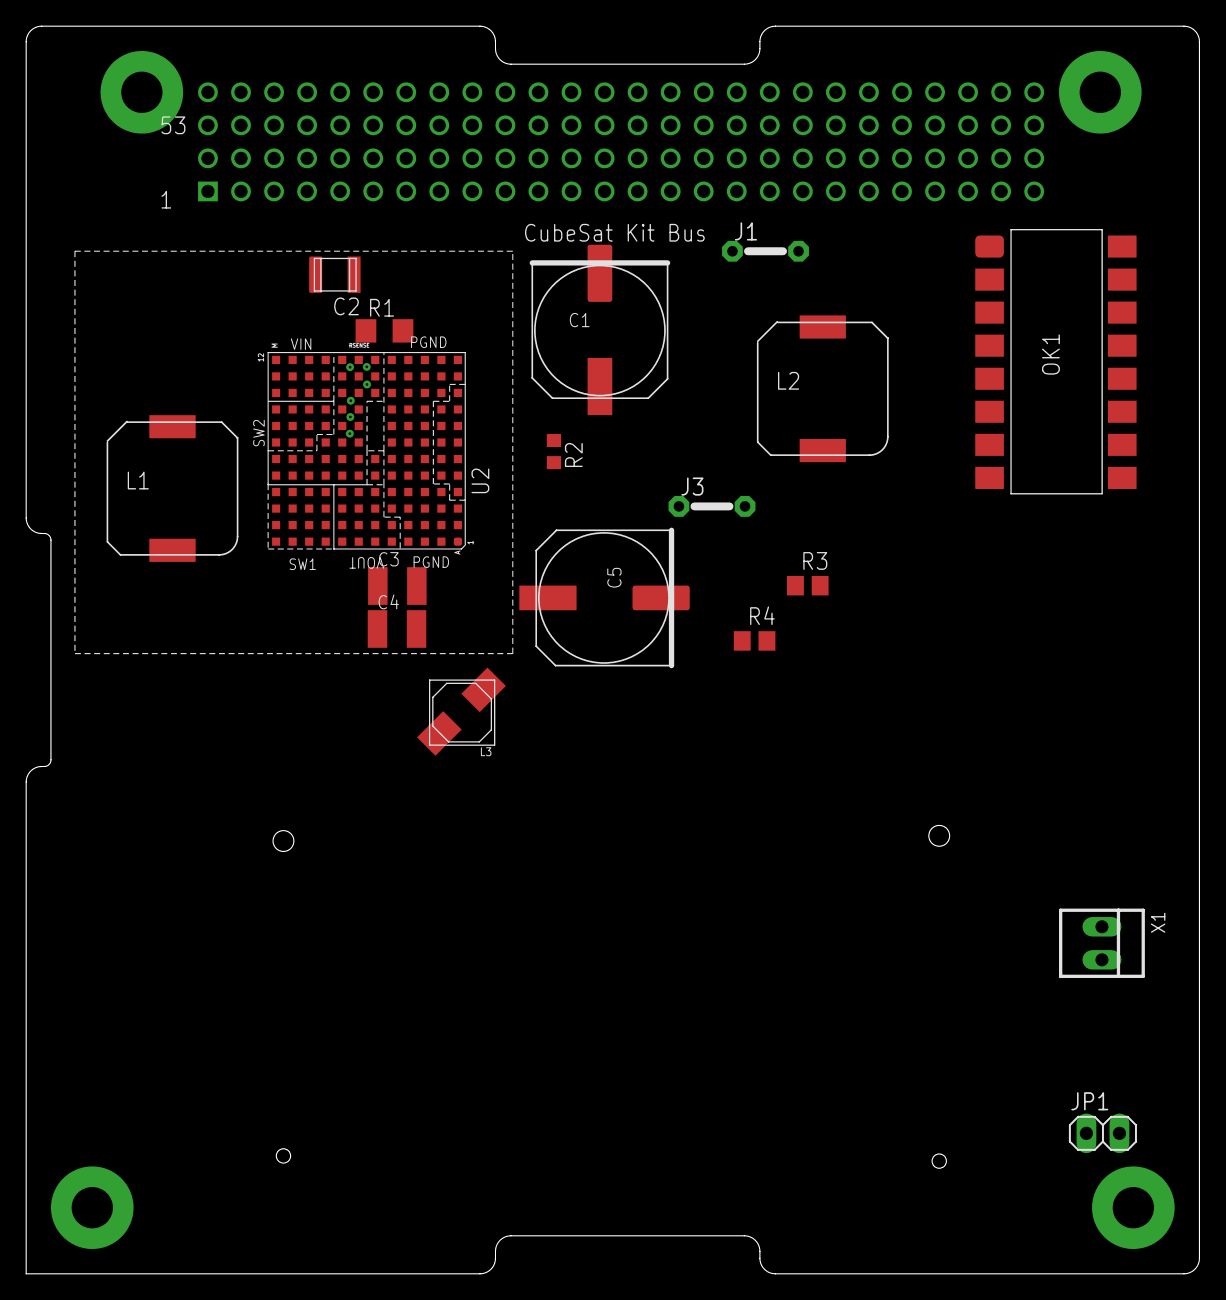
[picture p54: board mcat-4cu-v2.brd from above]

Board: 4 copper layers, 90.2 x 95.9 mm, 24 parts (1 on the bottom side), 18 nets.

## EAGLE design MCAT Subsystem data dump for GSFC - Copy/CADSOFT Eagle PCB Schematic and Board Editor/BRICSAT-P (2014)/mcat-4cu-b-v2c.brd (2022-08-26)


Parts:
J2: CSK-BUS-CONN2X2X26; CSK-BUS-PKG
J4: AMPMODU 5X2 SMT HDR; AMPMODU-SMT-PIN-HEADER-5X2
J8: M80-6810642; M80-68106

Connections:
GND: J2.81 (GND), J2.82 (GND), J2.83 (GND), J2.84 (GND), J4.1, J8.1, J8.2; also elsewhere on the board
I2C(CLK): J2.43 (SCL_SYS), J4.5; also elsewhere on the board
I2C(DATA): J2.41 (SDA_SYS), J4.4; also elsewhere on the board
P3_SW: J4.2, J8.4; also elsewhere on the board
PBATT_SW: J4.3, J8.5; also elsewhere on the board
SGND: J4.6; also elsewhere on the board
SW_TP1: J4.7; also elsewhere on the board
TP1_OUT: J4.8; also elsewhere on the board

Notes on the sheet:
I/F - CubeSatKit Bus Interface Section
Test Points
(c) Samudra Haque, The George Washington University, 2014. All Rights Reserved.
Power Connections from USNA EPS


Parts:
C1, C5: 68uF; OS-CON-SVPF-F12
C2: 4.7uF; MLCC-X7R-1210
C3, C4: 10uF; C1210K
H1, H2, H3: MOUNT-PAD-ROUNDCSK_MTG_HOLE_A5; CSK_MOUNTING_HOLE
HBL: MOUNT-PAD-ROUNDCSK_MTG_HOLE_A5; CSK_MOUNTING_HOLE
L1: 330 uH; MSS1048
L2: 33 uH; MSS1048
L3: 10 uH; SERIES-POWER-INDUCTORS
R1: 70 mOhms; R1206
R2: 4k7 0.1%; R0603
R3: 3K79; R0805
R4: 1K; R0805
SJ1, SJ2, SJ3, SJ4: SJ
U2: LTM4609MPV#PBF; LGA-141-LTC-05-08-1840-B

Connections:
GND: C1.K1 (K), C2.2, R2.1, SJ3.1, SJ4.1; also elsewhere on the board
INTVCC: R3.1, U2.A9 (FCB), U2.F5 (INTV_CC); also elsewhere on the board
unnamed: R2.2, U2.B6 (V_FB)
P3: SJ2.2; also elsewhere on the board
P3_SW: SJ2.1; also elsewhere on the board
PBATT_SW: SJ1.1; also elsewhere on the board
PGND: C3.2, C4.2, C5.K1 (K), H1.P$1, H2.P$1, H3.P$1, HBL.P$1, R1.2, SJ4.2, U2.A1 (PGND), U2.A2 (PGND), U2.A3 (PGND), U2.A5 (SENSE-), U2.A7 (SGND), U2.A11 (PGND), U2.A12 (PGND), U2.B1 (PGND), U2.B2 (PGND), U2.B3 (PGND), U2.B4 (PGND), U2.B10 (PGND), U2.B11 (PGND), U2.B12 (PGND), U2.C1 (PGND), U2.C2 (PGND), U2.C3 (PGND), U2.C4 (PGND), U2.C5 (PGND), U2.C6 (PGND), U2.C7 (PGND), U2.C8 (PGND), U2.C9 (PGND), U2.C10 (PGND), U2.C11 (PGND), U2.C12 (PGND), U2.D1 (PGND), U2.D2 (PGND), U2.D3 (PGND), U2.D4 (PGND), U2.D5 (PGND), U2.D6 (PGND), U2.D7 (PGND), U2.D8 (PGND), U2.D9 (PGND), U2.D10 (PGND), U2.D11 (PGND), U2.D12 (PGND), U2.E3 (PGND), U2.E4 (PGND), U2.E5 (PGND), U2.E6 (PGND), U2.E7 (PGND), U2.E8 (PGND), U2.E9 (PGND), U2.E10 (PGND), U2.E11 (PGND), U2.E12 (PGND); also elsewhere on the board
PGOOD_PMA: U2.B5 (PGOOD)
RSENSE: R1.1, U2.A4 (SENSE+), U2.F10 (R_SENSE), U2.F11 (R_SENSE), U2.F12 (R_SENSE), U2.G5 (R_SENSE), U2.G6 (R_SENSE), U2.G7 (R_SENSE), U2.G8 (R_SENSE), U2.G9 (R_SENSE), U2.G10 (R_SENSE), U2.G11 (R_SENSE), U2.G12 (R_SENSE), U2.H5 (R_SENSE), U2.H6 (R_SENSE), U2.H7 (R_SENSE), U2.H8 (R_SENSE), U2.H9 (R_SENSE), U2.H10 (R_SENSE), U2.H11 (R_SENSE), U2.H12 (R_SENSE), U2.J5 (R_SENSE), U2.J6 (R_SENSE), U2.J7 (R_SENSE), U2.K5 (R_SENSE), U2.K6 (R_SENSE), U2.L5 (R_SENSE), U2.L6 (R_SENSE), U2.M5 (R_SENSE), U2.M6 (R_SENSE)
RUN_PMA: U2.A8 (RUN)
SETFREQ: R3.2, R4.1, U2.B8 (PLLFLTR)
SGND: R4.2, SJ3.2; also elsewhere on the board
SW1: L1.2, U2.SW1@J1 (SW1), U2.SW1@J2 (SW1), U2.SW1@J3 (SW1), U2.SW1@J4 (SW1), U2.SW1@K1 (SW1), U2.SW1@K2 (SW1), U2.SW1@K3 (SW1), U2.SW1@K4 (SW1), U2.SW1@L1 (SW1), U2.SW1@L2 (SW1), U2.SW1@L3 (SW1), U2.SW1@L4 (SW1), U2.SW1@M1 (SW1), U2.SW1@M2 (SW1), U2.SW1@M3 (SW1), U2.SW1@M4 (SW1)
SW2: L1.1, U2.J8 (SW2), U2.J9 (SW2), U2.K7 (SW2), U2.K8 (SW2), U2.K9 (SW2), U2.L7 (SW2), U2.L8 (SW2), U2.L9 (SW2), U2.M7 (SW2), U2.M8 (SW2), U2.M9 (SW2)
VBATT_IN: C1.A1 (A), L2.1, SJ1.2
VIN: C2.1, L2.2, U2.J10 (V_IN), U2.J11 (V_IN), U2.J12 (V_IN), U2.K10 (V_IN), U2.K11 (V_IN), U2.K12 (V_IN), U2.L10 (V_IN), U2.L11 (V_IN), U2.L12 (V_IN), U2.M10 (V_IN), U2.M11 (V_IN), U2.M12 (V_IN)
VOUT: C3.1, C4.1, L3.1, U2.E1 (V_OUT), U2.E2 (V_OUT), U2.F1 (V_OUT), U2.F2 (V_OUT), U2.F3 (V_OUT), U2.F4 (V_OUT), U2.G1 (V_OUT), U2.G2 (V_OUT), U2.G3 (V_OUT), U2.G4 (V_OUT), U2.H2 (V_OUT), U2.H3 (V_OUT), U2.H4 (V_OUT), U2.VOUT (V_OUT)
VOUTA: C5.A1 (A), L3.2; also elsewhere on the board

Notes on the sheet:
PM - Power Management
Input Filter Network
SGND connected to PGND at output capacitor point
Output Filter Network
Switching Regulator f = 300 kHz Input = 6-36VDC (@7.2V, 1.56A) Output = 17.82VDC (@17.82VDC, 0.5A, max.) Ripple = 0.05 mVpp Discontinuous Current Mode (DCM) w/Constant Frequency
(c) Samudra Haque, The George Washington University, 2014. All Rights Reserved.
NOTE 3: PGOOD_PMA signal umonitored in this rev. RUN_PMA is Inhibit #4 controlled by MTCU SW
Switching Power Regulation
To PD Ch. 1-4, L/H 17.9VDC @0.5A nom. (max.)
From Interface Switched S/C Batt. Power I/P 6-36VDC VBATT_IN is Inhibit #3 controlled by PBATT_SW supply switch of host S/C


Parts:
OK3: PS2501L-4
R33: 1K; R0805
R34: 604R; R0805
U1: UCAT-4CU-B-CONTROL-UNITNANO55415; MOLEX-MINI-PCI-EXPRESS-8MM-52CKT

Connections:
GND: U1.18 (GND), U1.48 (GND); also elsewhere on the board
I2C(CLK): U1.27 (I2C0_SCL); also elsewhere on the board
I2C(DATA): U1.29 (I2C0_SDA); also elsewhere on the board
INTVCC: R34.2; also elsewhere on the board
unnamed: OK3.1 (A1), R33.2
P3: R33.1, U1.17 (VCC3V), U1.47 (VCC3V); also elsewhere on the board
SGND: OK3.15 (E1); also elsewhere on the board
SW_P18H1: U1.35 (SDHC_DAT0); also elsewhere on the board
SW_P18H2: U1.34 (UART1_TX); also elsewhere on the board
SW_P18H3: U1.33 (SDHC_CMD); also elsewhere on the board
SW_P18H4: U1.32 (UART1_RX); also elsewhere on the board
SW_P18L1: U1.39 (SDHC_DAT2); also elsewhere on the board
SW_P18L2: U1.38 (UART1_CTS); also elsewhere on the board
SW_P18L3: U1.37 (SDHC_DAT1); also elsewhere on the board
SW_P18L4: U1.36 (UART1_RTS); also elsewhere on the board
SW_RUNPMA: U1.23 (T2IN)
SW_TP1: OK3.2 (K1), U1.31 (SDHC_CLK); also elsewhere on the board
TP1_OUT: OK3.16 (C1), R34.1; also elsewhere on the board

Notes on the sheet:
CU - Control Unit Section
SW_P18L1/39/PF1 SW_P18L2/38/PE2/RGPIO7 SW_P18L3/37/PF0 SW_P18L4/36/PE1/RGPIO8 SW_P18H1/35/PG7 SW_P18H2/34/PF7 SW_P18H3/33/PG6 SW_P18H4/32/PE0 SW_TP1/31/PG5 SW_RUNPMA/23/PD1/RGPIO2
(c) Samudra Haque, The George Washington University, 2014. All Rights Reserved.
Microcontroller Module (Mini-PCI Express Conn.)
Common Trigger Pulse Distribution to 4xPPU Ch.
NOTE XX: Future version will have multiple trigger pulses
Microcontroller Module (GPIO Control Line Assignment)


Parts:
OK1, OK2: PS2501L-4
R5, R6, R7, R8, R9, R10, R11, R12: 5K42 0.1%; R1206
R13, R14, R15, R16, R17, R18, R19, R20: 100K 0.1%; R0402
R21, R22, R23, R25, R26, R27: 51K 0.1%; R0603
R24, R28: 51k 0.1%; R0603
R29, R30, R31, R32: 0.1R 1% PTC; R0402
U3, U4: LT1161ISW; 20-LEAD-PLASTIC-SO

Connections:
CH1HG: U3.16 (GATE2); also elsewhere on the board
CH1LG: U3.18 (GATE1); also elsewhere on the board
CH1S: R29.1; also elsewhere on the board
CH2HG: U3.12 (GATE4); also elsewhere on the board
CH2LG: U3.14 (GATE3); also elsewhere on the board
CH2S: R30.1; also elsewhere on the board
CH3HG: U4.16 (GATE2); also elsewhere on the board
CH3LG: U4.18 (GATE1); also elsewhere on the board
CH3S: R31.1; also elsewhere on the board
CH4HG: U4.12 (GATE4); also elsewhere on the board
CH4LG: U4.14 (GATE3); also elsewhere on the board
CH4S: R32.1; also elsewhere on the board
unnamed: OK1.16 (C1), R13.2
unnamed: OK1.14 (C2), R14.2
unnamed: OK1.12 (C3), R15.2
unnamed: OK1.10 (C4), R16.2
unnamed: OK2.16 (C1), R17.2
unnamed: OK2.14 (C2), R18.2
unnamed: OK2.12 (C3), R19.2
unnamed: OK2.10 (C4), R20.2
OK1E1: OK1.15 (E1), R25.2, U3.3 (INPUT1)
OK1E2: OK1.13 (E2), R26.2, U3.5 (INPUT2)
OK1E3: OK1.11 (E3), R27.2, U3.7 (INPUT3)
OK1E4: OK1.9 (E4), R28.2, U3.9 (INPUT4)
OK2E1: OK2.15 (E1), R21.2, U4.3 (INPUT1)
OK2E2: OK2.13 (E2), R22.2, U4.5 (INPUT2)
OK2E3: OK2.11 (E3), R23.2, U4.7 (INPUT3)
OK2E4: OK2.9 (E4), R24.2, U4.9 (INPUT4)
P18_SW1: OK1.1 (A1), R5.1
P18_SW2: OK1.5 (A3), R6.1
P18_SW3: OK2.1 (A1), R7.1
P18_SW4: OK2.5 (A3), R8.1
P18_SW5: OK1.3 (A2), R9.1
P18_SW6: OK1.7 (A4), R10.1
P18_SW7: OK2.3 (A2), R11.1
P18_SW8: OK2.7 (A4), R12.1
PGND: R21.1, R22.1, R23.1, R24.1, R25.1, R26.1, R27.1, R28.1, U3.1 (GND), U3.10 (GND), U4.1 (GND), U4.10 (GND); also elsewhere on the board
SGND: OK1.2 (K1), OK1.4 (K2), OK1.6 (K3), OK1.8 (K4), OK2.2 (K1), OK2.4 (K2), OK2.6 (K3), OK2.8 (K4); also elsewhere on the board
SW_P18H1: R9.2; also elsewhere on the board
SW_P18H2: R10.2; also elsewhere on the board
SW_P18H3: R11.2; also elsewhere on the board
SW_P18H4: R12.2; also elsewhere on the board
SW_P18L1: R5.2; also elsewhere on the board
SW_P18L2: R6.2; also elsewhere on the board
SW_P18L3: R7.2; also elsewhere on the board
SW_P18L4: R8.2; also elsewhere on the board
VOUTA: R13.1, R14.1, R15.1, R16.1, R17.1, R18.1, R19.1, R20.1, R29.2, R30.2, R31.2, R32.2, U3.11 (V+), U3.13 (SENSE4), U3.15 (SENSE3), U3.17 (SENSE2), U3.19 (SENSE1), U3.20 (V+), U4.11 (V+), U4.13 (SENSE4), U4.15 (SENSE3), U4.17 (SENSE2), U4.19 (SENSE1), U4.20 (V+); also elsewhere on the board

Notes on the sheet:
PD - Power Distribution Section Part 1/2
NOTE 1 Current Limit functionality (SENSEx) for LT1161 channels CHnnnnH not implemented in this revision pending determination of over current limit NOTE 2 dv/dt control network for LT1161 Gates not implemented pending further review
SEE NOTE 1
(c) Samudra Haque, The George Washington University, 2014. All Rights Reserved.
From CU
To PD Gate Drives Ch. 1/2
To PD High Current Supply for Ch1-4 P18H
To PD Gate Drives Ch. 3/4


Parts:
J5, J6: M80-6811242; M80-68112
Q9, Q10, Q11, Q12, Q13, Q14, Q15, Q16: SI5404BDC; 1206-8-CHIPFET

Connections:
CH1HG: Q10.G; also elsewhere on the board
CH1LG: Q9.G; also elsewhere on the board
CH1S: Q10.D; also elsewhere on the board
CH1_P18H: J5.8, Q10.S
CH1_P18L: J5.7, Q9.S
CH2HG: Q12.G; also elsewhere on the board
CH2LG: Q11.G; also elsewhere on the board
CH2S: Q12.D; also elsewhere on the board
CH2_P18H: J5.11, Q12.S
CH2_P18L: J5.10, Q11.S
CH3HG: Q14.G; also elsewhere on the board
CH3LG: Q13.G; also elsewhere on the board
CH3S: Q14.D; also elsewhere on the board
CH3_P18H: J6.8, Q14.S
CH3_P18L: J6.7, Q13.S
CH4HG: Q16.G; also elsewhere on the board
CH4LG: Q15.G; also elsewhere on the board
CH4S: Q16.D; also elsewhere on the board
CH4_P18H: J6.11, Q16.S
CH4_P18L: J6.10, Q15.S
PGND: J5.1, J5.4, J6.1, J6.4; also elsewhere on the board
SGND: J5.9, J5.12, J6.9, J6.12; also elsewhere on the board
TP1_OUT: J5.3, J5.6, J6.3, J6.6; also elsewhere on the board
VOUTA: Q9.D, Q11.D, Q13.D, Q15.D; also elsewhere on the board

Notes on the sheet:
PD - Power Distribution Section Part 2/2
(c) Samudra Haque, The George Washington University, 2014. All Rights Reserved.
See Note 2
To Upper Thruster PCB Ch. 1/2
To Lower Thruster PCB Ch. 3/4

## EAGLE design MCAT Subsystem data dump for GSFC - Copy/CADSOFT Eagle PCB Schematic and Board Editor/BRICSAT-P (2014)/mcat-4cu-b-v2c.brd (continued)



Board: 4 copper layers, 90.2 x 95.9 mm, 70 parts (30 on the bottom side), 73 nets.

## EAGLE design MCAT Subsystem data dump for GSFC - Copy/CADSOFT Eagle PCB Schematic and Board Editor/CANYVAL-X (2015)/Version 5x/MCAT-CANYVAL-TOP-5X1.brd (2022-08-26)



Board: 6 copper layers, 87.9 x 95.0 mm, 55 parts (48 on the bottom side), 72 nets.

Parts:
B8: MCAT-4CU-C-PCB/TOP; MCAT-4CU-C-TOP-V4-BLANK
CT-V2L1-1:BC3, CT-V2L1-1:BC5: BYPASS-CAP-1UF; 0612-REV
CT-V2L1-1:BC4, CT-V2L1-1:BC6: BYPASS-CAP-0.1UF; 0612-REV
CT-V2L1-1:J7: MOLEX-78171-5007
CT-V2L1-1:JMP1: 0R-JUMPA; A0R-JMP
CT-V2L1-1:R1, CT-V2L1-1:R2, CT-V2L1-1:R3: 10k; R0402
CT-V2L1-1:U1: PCA9512ADP; SOT505-1
F4, F5, F6, F7: SMTRAM2-6-5; SMTRA-M2-6-5
GBUS-TOP1:G1, GBUS-TOP1:G2: HIROSE-FH40-60S-0.5SV
GBUS-TOP1:H1: H1-H5-INBOARD-CSK-BUS-CONN; CONN-2X26X0.1-HDR
GBUS-TOP1:H2: H2-H6-OUTBOARD-CSK-BUS-CONN; CONN-2X26X0.1-HDR
J2: MOLEX-502598-5193
PM-V2L2-1:BC1, PM-V2L2-1:BC3: BYPASS-CAP-0.1UF; 0612-REV
PM-V2L2-1:BC2, PM-V2L2-1:BC4: BYPASS-CAP-1UF; 0612-REV
PM-V2L2-1:C1, PM-V2L2-1:C5: 68uF; OS-CON-SVPF-F12
PM-V2L2-1:C2: 4.7uF; MLCC-X7R-1210
PM-V2L2-1:C3, PM-V2L2-1:C4: 10uF; C1210K
PM-V2L2-1:C6: 10u; C1210
PM-V2L2-1:C7: 10u; C1206
PM-V2L2-1:C8, PM-V2L2-1:C10: 10n; C0402
PM-V2L2-1:C9: 3.3u; C0805
PM-V2L2-1:L1: 33uH; MSS1048
PM-V2L2-1:L2: 68uH; MSS1048
PM-V2L2-1:L3: 10uH; SERIES-POWER-INDUCTORS
PM-V2L2-1:R1: 2K; R0402
PM-V2L2-1:R2: 1K; R0402
PM-V2L2-1:R3: 27mOhms; R0805
PM-V2L2-1:R4: 4k70.1%; R0603
PM-V2L2-1:R5, PM-V2L2-1:R6: 1M; R0402
PM-V2L2-1:R7: 357K; R1206
PM-V2L2-1:R8: 210K; R0402
PM-V2L2-1:R9: 619K; R0805
PM-V2L2-1:R10: 200K; R0402
PM-V2L2-1:SJ3, PM-V2L2-1:SJ4, PM-V2L2-1:SJ6: 0R; R0805
PM-V2L2-1:TP1, PM-V2L2-1:TP2, PM-V2L2-1:TP4: PCB-MINI-SMD-TESTPOINT/SQ; PCB-MINI-SMD-TESTPOINT
PM-V2L2-1:U1: LTM4609MPV#PBF; LGA-141-LTC-05-08-1840-B
PM-V2L2-1:U2: LT3030MPFE#PBF; TSSOP20-FE-CB

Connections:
CT-V2L1-1:I2C_VCC: CT-V2L1-1:BC5.1, CT-V2L1-1:BC6.1, CT-V2L1-1:JMP1.2, CT-V2L1-1:U1.8
CT-V2L1-1:N$2: CT-V2L1-1:R2.1, CT-V2L1-1:U1.5
GBUS-TOP1:G-H1-1: GBUS-TOP1:G2.2, GBUS-TOP1:H1.1
GBUS-TOP1:G-H1-2: GBUS-TOP1:G2.3, GBUS-TOP1:H1.2
GBUS-TOP1:G-H1-3: GBUS-TOP1:G2.4, GBUS-TOP1:H1.3
GBUS-TOP1:G-H1-9: GBUS-TOP1:G2.5, GBUS-TOP1:H1.9
GBUS-TOP1:G-H1-10: GBUS-TOP1:G2.6, GBUS-TOP1:H1.10
GBUS-TOP1:G-H1-11: GBUS-TOP1:G2.7, GBUS-TOP1:H1.11
GBUS-TOP1:G-H1-12: GBUS-TOP1:G2.8, GBUS-TOP1:H1.12
GBUS-TOP1:G-H1-13: GBUS-TOP1:G2.9, GBUS-TOP1:H1.13
GBUS-TOP1:G-H1-14: GBUS-TOP1:G2.10, GBUS-TOP1:H1.14
GBUS-TOP1:G-H1-18: GBUS-TOP1:G2.28, GBUS-TOP1:H1.18
GBUS-TOP1:G-H1-19: GBUS-TOP1:G1.28, GBUS-TOP1:H1.19
GBUS-TOP1:G-H1-20: GBUS-TOP1:G1.29, GBUS-TOP1:H1.20
GBUS-TOP1:G-H1-21: GBUS-TOP1:G2.34, GBUS-TOP1:H1.21
GBUS-TOP1:G-H1-22: GBUS-TOP1:G2.35, GBUS-TOP1:H1.22
GBUS-TOP1:G-H1-23: GBUS-TOP1:G2.36, GBUS-TOP1:H1.23
GBUS-TOP1:G-H1-24: GBUS-TOP1:G2.11, GBUS-TOP1:H1.24
GBUS-TOP1:G-H1-26: GBUS-TOP1:G2.29, GBUS-TOP1:H1.26
GBUS-TOP1:G-H1-29: GBUS-TOP1:G2.30, GBUS-TOP1:H1.29
GBUS-TOP1:G-H1-33: GBUS-TOP1:G2.32, GBUS-TOP1:H1.33
GBUS-TOP1:G-H1-35: GBUS-TOP1:G2.33, GBUS-TOP1:H1.35
GBUS-TOP1:G-H1-45: GBUS-TOP1:G2.14, GBUS-TOP1:H1.45
GBUS-TOP1:G-H1-47: GBUS-TOP1:G2.15, GBUS-TOP1:H1.47
GBUS-TOP1:G-H1-49: GBUS-TOP1:G2.31, GBUS-TOP1:H1.49
GBUS-TOP1:G-H2-50: GBUS-TOP1:G2.1, GBUS-TOP1:H2.50
GBUS-TOP1:M-3V3-BUS: GBUS-TOP1:G1.10, GBUS-TOP1:G1.11, GBUS-TOP1:G1.12, GBUS-TOP1:G1.13, GBUS-TOP1:G1.14, GBUS-TOP1:G1.15, GBUS-TOP1:G1.16, GBUS-TOP1:G1.17, GBUS-TOP1:G1.18, GBUS-TOP1:H2.27, GBUS-TOP1:H2.28
GBUS-TOP1:M-5V-BUS: GBUS-TOP1:G1.1, GBUS-TOP1:G1.2, GBUS-TOP1:G1.3, GBUS-TOP1:G1.4, GBUS-TOP1:G1.5, GBUS-TOP1:G1.6, GBUS-TOP1:G1.7, GBUS-TOP1:G1.8, GBUS-TOP1:G1.9, GBUS-TOP1:H2.25, GBUS-TOP1:H2.26
GBUS-TOP1:M-5V-USB-CHG: GBUS-TOP1:G1.48, GBUS-TOP1:H1.32
GBUS-TOP1:M-12V-BUS: GBUS-TOP1:G2.58, GBUS-TOP1:G2.59, GBUS-TOP1:G2.60, GBUS-TOP1:H2.23, GBUS-TOP1:H2.24
GBUS-TOP1:M-SW2-12V: GBUS-TOP1:G2.40, GBUS-TOP1:G2.41, GBUS-TOP1:H2.10
GBUS-TOP1:M-SW3-BAT: GBUS-TOP1:G2.42, GBUS-TOP1:G2.43, GBUS-TOP1:H2.11
GBUS-TOP1:M-SW4-BAT: GBUS-TOP1:G2.44, GBUS-TOP1:G2.45, GBUS-TOP1:H2.12
GBUS-TOP1:M-SW5-5V: GBUS-TOP1:G2.46, GBUS-TOP1:G2.47, GBUS-TOP1:H2.13
GBUS-TOP1:M-SW6-5V: GBUS-TOP1:G2.48, GBUS-TOP1:G2.49, GBUS-TOP1:H2.15
GBUS-TOP1:M-SW7-5V: GBUS-TOP1:G2.50, GBUS-TOP1:G2.51, GBUS-TOP1:H2.16
GBUS-TOP1:M-SW8-3V3: GBUS-TOP1:G2.52, GBUS-TOP1:G2.53, GBUS-TOP1:H2.18
GBUS-TOP1:M-SW9-3V3: GBUS-TOP1:G2.54, GBUS-TOP1:G2.55, GBUS-TOP1:H2.19
GBUS-TOP1:M-SW10-3V3: GBUS-TOP1:G2.56, GBUS-TOP1:G2.57, GBUS-TOP1:H2.20
GBUS-TOP1:RBF_SW: GBUS-TOP1:G1.30, GBUS-TOP1:G1.60, GBUS-TOP1:H2.37, GBUS-TOP1:H2.38
GBUS-TOP1:SEP_SW1: GBUS-TOP1:G1.58, GBUS-TOP1:H2.39
GBUS-TOP1:SEP_SW2: GBUS-TOP1:G1.59, GBUS-TOP1:H2.40
GND: B8.GND, B8.GND@1, B8.GND@2, B8.GND@3, B8.GND@4, B8.GND@6, CT-V2L1-1:BC3.2, CT-V2L1-1:BC4.2, CT-V2L1-1:BC5.2, CT-V2L1-1:BC6.2, CT-V2L1-1:J7.5, CT-V2L1-1:U1.4, GBUS-TOP1:G1.19, GBUS-TOP1:G1.20, GBUS-TOP1:G1.21, GBUS-TOP1:G1.22, GBUS-TOP1:G1.23, GBUS-TOP1:G1.24, GBUS-TOP1:G1.25, GBUS-TOP1:G1.26, GBUS-TOP1:G1.27, GBUS-TOP1:G1.31, GBUS-TOP1:G1.32, GBUS-TOP1:G1.33, GBUS-TOP1:G1.34, GBUS-TOP1:G1.35, GBUS-TOP1:G1.36, GBUS-TOP1:G1.37, GBUS-TOP1:G1.38, GBUS-TOP1:G1.39, GBUS-TOP1:G1.40, GBUS-TOP1:G1.41, GBUS-TOP1:G1.42, GBUS-TOP1:G1.43, GBUS-TOP1:G1.44, GBUS-TOP1:G1.45, GBUS-TOP1:G1.46, GBUS-TOP1:G1.47, GBUS-TOP1:G2.16, GBUS-TOP1:G2.17, GBUS-TOP1:G2.18, GBUS-TOP1:G2.19, GBUS-TOP1:G2.20, GBUS-TOP1:G2.21, GBUS-TOP1:G2.22, GBUS-TOP1:G2.23, GBUS-TOP1:G2.24, GBUS-TOP1:G2.25, GBUS-TOP1:G2.26, GBUS-TOP1:G2.27, GBUS-TOP1:G2.37, GBUS-TOP1:H2.9, GBUS-TOP1:H2.14, GBUS-TOP1:H2.17, GBUS-TOP1:H2.21, GBUS-TOP1:H2.22, GBUS-TOP1:H2.29, GBUS-TOP1:H2.30, GBUS-TOP1:H2.32, GBUS-TOP1:H2.47, GBUS-TOP1:H2.48, J2.2, J2.4, J2.6, J2.8, J2.10, J2.12, J2.14, J2.16, J2.18, J2.20, J2.22, J2.24, PM-V2L2-1:BC1.2, PM-V2L2-1:BC2.2, PM-V2L2-1:BC3.2, PM-V2L2-1:BC4.2, PM-V2L2-1:C1.K1, PM-V2L2-1:C2.2, PM-V2L2-1:C3.2, PM-V2L2-1:C4.2, PM-V2L2-1:C5.K1, PM-V2L2-1:C6.2, PM-V2L2-1:C7.2, PM-V2L2-1:C9.2, PM-V2L2-1:R3.2, PM-V2L2-1:R4.1, PM-V2L2-1:R8.1, PM-V2L2-1:R10.1, PM-V2L2-1:SJ3.1, PM-V2L2-1:SJ4.1, PM-V2L2-1:U1.A1, PM-V2L2-1:U1.A2, PM-V2L2-1:U1.A3, PM-V2L2-1:U1.A5, PM-V2L2-1:U1.A11, PM-V2L2-1:U1.A12, PM-V2L2-1:U1.B1, PM-V2L2-1:U1.B2, PM-V2L2-1:U1.B3, PM-V2L2-1:U1.B4, PM-V2L2-1:U1.B10, PM-V2L2-1:U1.B11, PM-V2L2-1:U1.B12, PM-V2L2-1:U1.C1, PM-V2L2-1:U1.C2, PM-V2L2-1:U1.C3, PM-V2L2-1:U1.C4, PM-V2L2-1:U1.C5, PM-V2L2-1:U1.C6, PM-V2L2-1:U1.C7, PM-V2L2-1:U1.C8, PM-V2L2-1:U1.C9, PM-V2L2-1:U1.C10, PM-V2L2-1:U1.C11, PM-V2L2-1:U1.C12, PM-V2L2-1:U1.D1, PM-V2L2-1:U1.D2, PM-V2L2-1:U1.D3, PM-V2L2-1:U1.D4, PM-V2L2-1:U1.D5, PM-V2L2-1:U1.D6, PM-V2L2-1:U1.D7, PM-V2L2-1:U1.D8, PM-V2L2-1:U1.D9, PM-V2L2-1:U1.D10, PM-V2L2-1:U1.D11, PM-V2L2-1:U1.D12, PM-V2L2-1:U1.E3, PM-V2L2-1:U1.E4, PM-V2L2-1:U1.E5, PM-V2L2-1:U1.E6, PM-V2L2-1:U1.E7, PM-V2L2-1:U1.E8, PM-V2L2-1:U1.E9, PM-V2L2-1:U1.E10, PM-V2L2-1:U1.E11, PM-V2L2-1:U1.E12, PM-V2L2-1:U2.5, PM-V2L2-1:U2.6, PM-V2L2-1:U2.15, PM-V2L2-1:U2.16, PM-V2L2-1:U2.21
MCAT_SCL: CT-V2L1-1:R3.1, CT-V2L1-1:U1.2, J2.50
MCAT_SDA: CT-V2L1-1:R1.1, CT-V2L1-1:U1.7, J2.49
P3: CT-V2L1-1:BC3.1, CT-V2L1-1:BC4.1, CT-V2L1-1:JMP1.1, CT-V2L1-1:R1.2, CT-V2L1-1:R2.2, CT-V2L1-1:R3.2, CT-V2L1-1:U1.1, J2.21, J2.23, PM-V2L2-1:C7.1, PM-V2L2-1:C8.1, PM-V2L2-1:R7.2, PM-V2L2-1:TP1.1, PM-V2L2-1:U2.3, PM-V2L2-1:U2.4
P5: CT-V2L1-1:JMP1.3, PM-V2L2-1:C9.1, PM-V2L2-1:C10.1, PM-V2L2-1:R9.2, PM-V2L2-1:TP2.1, PM-V2L2-1:U2.7, PM-V2L2-1:U2.8
P12_IN: CT-V2L1-1:J7.2, GBUS-TOP1:G2.38, GBUS-TOP1:G2.39, GBUS-TOP1:H2.8, PM-V2L2-1:BC1.1, PM-V2L2-1:BC2.1, PM-V2L2-1:C6.1, PM-V2L2-1:R5.2, PM-V2L2-1:R6.2, PM-V2L2-1:U2.11, PM-V2L2-1:U2.13, PM-V2L2-1:U2.14, PM-V2L2-1:U2.17, PM-V2L2-1:U2.18, PM-V2L2-1:U2.20
PGOOD_PMA: CT-V2L1-1:J7.3, PM-V2L2-1:U1.B5
PM-V2L2-1:ADJ1: PM-V2L2-1:R7.1, PM-V2L2-1:R8.2, PM-V2L2-1:U2.1
PM-V2L2-1:ADJ2: PM-V2L2-1:R9.1, PM-V2L2-1:R10.2, PM-V2L2-1:U2.10
PM-V2L2-1:BYP1: PM-V2L2-1:C8.2, PM-V2L2-1:U2.2
PM-V2L2-1:BYP2: PM-V2L2-1:C10.2, PM-V2L2-1:U2.9
PM-V2L2-1:INTVCC: PM-V2L2-1:R1.1, PM-V2L2-1:U1.A9, PM-V2L2-1:U1.F5
PM-V2L2-1:P18_OUT: PM-V2L2-1:C5.A1, PM-V2L2-1:L3.2, PM-V2L2-1:SJ6.1
PM-V2L2-1:PWRDGD2: PM-V2L2-1:R6.1, PM-V2L2-1:U2.12
PM-V2L2-1:PWRGD1: PM-V2L2-1:R5.1, PM-V2L2-1:U2.19
PM-V2L2-1:RSENSE: PM-V2L2-1:R3.1, PM-V2L2-1:U1.A4, PM-V2L2-1:U1.F10, PM-V2L2-1:U1.F11, PM-V2L2-1:U1.F12, PM-V2L2-1:U1.G5, PM-V2L2-1:U1.G6, PM-V2L2-1:U1.G7, PM-V2L2-1:U1.G8, PM-V2L2-1:U1.G9, PM-V2L2-1:U1.G10, PM-V2L2-1:U1.G11, PM-V2L2-1:U1.G12, PM-V2L2-1:U1.H5, PM-V2L2-1:U1.H6, PM-V2L2-1:U1.H7, PM-V2L2-1:U1.H8, PM-V2L2-1:U1.H9, PM-V2L2-1:U1.H10, PM-V2L2-1:U1.H11, PM-V2L2-1:U1.H12, PM-V2L2-1:U1.J5, PM-V2L2-1:U1.J6, PM-V2L2-1:U1.J7, PM-V2L2-1:U1.K5, PM-V2L2-1:U1.K6, PM-V2L2-1:U1.L5, PM-V2L2-1:U1.L6, PM-V2L2-1:U1.M5, PM-V2L2-1:U1.M6
PM-V2L2-1:SETFREQ: PM-V2L2-1:R1.2, PM-V2L2-1:R2.1, PM-V2L2-1:U1.B8
PM-V2L2-1:SGND: PM-V2L2-1:R2.2, PM-V2L2-1:SJ3.2, PM-V2L2-1:SJ4.2, PM-V2L2-1:U1.A7
PM-V2L2-1:SW1: PM-V2L2-1:L2.2, PM-V2L2-1:U1.SW1@J1, PM-V2L2-1:U1.SW1@J2, PM-V2L2-1:U1.SW1@J3, PM-V2L2-1:U1.SW1@J4, PM-V2L2-1:U1.SW1@K1, PM-V2L2-1:U1.SW1@K2, PM-V2L2-1:U1.SW1@K3, PM-V2L2-1:U1.SW1@K4, PM-V2L2-1:U1.SW1@L1, PM-V2L2-1:U1.SW1@L2, PM-V2L2-1:U1.SW1@L3, PM-V2L2-1:U1.SW1@L4, PM-V2L2-1:U1.SW1@M1, PM-V2L2-1:U1.SW1@M2, PM-V2L2-1:U1.SW1@M3, PM-V2L2-1:U1.SW1@M4
PM-V2L2-1:SW2: PM-V2L2-1:L2.1, PM-V2L2-1:U1.J8, PM-V2L2-1:U1.J9, PM-V2L2-1:U1.K7, PM-V2L2-1:U1.K8, PM-V2L2-1:U1.K9, PM-V2L2-1:U1.L7, PM-V2L2-1:U1.L8, PM-V2L2-1:U1.L9, PM-V2L2-1:U1.M7, PM-V2L2-1:U1.M8, PM-V2L2-1:U1.M9
PM-V2L2-1:VFB: PM-V2L2-1:R4.2, PM-V2L2-1:U1.B6
PM-V2L2-1:VIN: PM-V2L2-1:C2.1, PM-V2L2-1:L1.2, PM-V2L2-1:U1.J10, PM-V2L2-1:U1.J11, PM-V2L2-1:U1.J12, PM-V2L2-1:U1.K10, PM-V2L2-1:U1.K11, PM-V2L2-1:U1.K12, PM-V2L2-1:U1.L10, PM-V2L2-1:U1.L11, PM-V2L2-1:U1.L12, PM-V2L2-1:U1.M10, PM-V2L2-1:U1.M11, PM-V2L2-1:U1.M12
PM-V2L2-1:VOUT: PM-V2L2-1:C3.1, PM-V2L2-1:C4.1, PM-V2L2-1:L3.1, PM-V2L2-1:U1.E1, PM-V2L2-1:U1.E2, PM-V2L2-1:U1.F1, PM-V2L2-1:U1.F2, PM-V2L2-1:U1.F3, PM-V2L2-1:U1.F4, PM-V2L2-1:U1.G1, PM-V2L2-1:U1.G2, PM-V2L2-1:U1.G3, PM-V2L2-1:U1.G4, PM-V2L2-1:U1.H2, PM-V2L2-1:U1.H3, PM-V2L2-1:U1.H4, PM-V2L2-1:U1.VOUT
SCLIN: CT-V2L1-1:U1.3, GBUS-TOP1:G2.13, GBUS-TOP1:H1.43
SDAIN: CT-V2L1-1:U1.6, GBUS-TOP1:G2.12, GBUS-TOP1:H1.41
SW_RUNPMA: J2.25, PM-V2L2-1:U1.A8
UART0_RX: CT-V2L1-1:J7.6, J2.48
UART0_TX: CT-V2L1-1:J7.7, J2.47
VBATT_IN: CT-V2L1-1:J7.1, GBUS-TOP1:G1.49, GBUS-TOP1:G1.50, GBUS-TOP1:G1.51, GBUS-TOP1:G1.52, GBUS-TOP1:G1.53, GBUS-TOP1:G1.54, GBUS-TOP1:G1.55, GBUS-TOP1:G1.56, GBUS-TOP1:G1.57, GBUS-TOP1:H2.45, GBUS-TOP1:H2.46, PM-V2L2-1:BC3.1, PM-V2L2-1:BC4.1, PM-V2L2-1:C1.A1, PM-V2L2-1:L1.1
VOUTA: J2.1, J2.3, J2.5, J2.7, J2.9, J2.11, J2.13, J2.15, J2.17, J2.19, PM-V2L2-1:SJ6.2, PM-V2L2-1:TP4.1

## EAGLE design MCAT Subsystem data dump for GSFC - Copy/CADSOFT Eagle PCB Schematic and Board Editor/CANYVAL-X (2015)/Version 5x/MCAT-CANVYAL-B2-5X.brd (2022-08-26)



Board: 6 copper layers, 83.9 x 18.6 mm, 5 parts (2 on the bottom side), 5 nets.

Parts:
B3: MCAT-4CU-C-PCB/MID; MCAT-4CU-C-MID-V4-BLANK
F1, F7: SMTRAM2-6-5; SMTRA-M2-6-5
THL2:TH2: MCAT-TH-G4X-YONSEI/LH; MCAT-TH-G4X-LH
THR1:TH2: MCAT-TH-G4X-YONSEI/RH; MCAT-TH-G4X-RH

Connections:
GND: B3.GND, B3.GND@2, B3.GND@3
unnamed: THR1:TH2.K, THR1:TH2.MCOUT
unnamed: THL2:TH2.K, THL2:TH2.MCOUT
THL2:KTMMCIN: THL2:TH2.KTM, THL2:TH2.MCIN
THR1:KTMMCIN: THR1:TH2.KTM, THR1:TH2.MCIN

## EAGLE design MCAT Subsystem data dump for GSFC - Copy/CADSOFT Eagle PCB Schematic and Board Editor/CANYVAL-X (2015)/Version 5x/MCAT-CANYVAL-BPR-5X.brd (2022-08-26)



Board: 6 copper layers, 71.5 x 61.0 mm, 40 parts (5 on the bottom side), 17 nets.

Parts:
B1: MCAT-4CU-C-PCB/BPR; MCAT-4CU-C-BPR-V4-BLANK
F1, F2, F3, F4, F5, F7: SMTRAM2-6-5-RA; SMTRA-M2-6-5-RA
J4: MOLEX-502598-5193
PPU-V8C1-2:BC1, PPU-V8C1-2:BC3, PPU-V8C1-4:BC1, PPU-V8C1-4:BC3: BYPASS-CAP-0.1UF; 0612-REV
PPU-V8C1-2:BC2, PPU-V8C1-2:BC4, PPU-V8C1-4:BC2, PPU-V8C1-4:BC4: BYPASS-CAP-1UF; 0612-REV
PPU-V8C1-2:C1, PPU-V8C1-4:C1: 680uF/20WV; CHEMI-CON-PSG-JB5
PPU-V8C1-2:CT1, PPU-V8C1-4:CT1: MURATA-5600-CURR-XFR/RA; MURATA-5600-SERIES-CURR-XFR-RA
PPU-V8C1-2:L1, PPU-V8C1-4:L1: PPUV8-INDUCTOR-V2
PPU-V8C1-2:Q11, PPU-V8C1-4:Q11: IXYH30N120C3D1; IXYS-TO-247-AD-VERT
PPU-V8C1-2:R1, PPU-V8C1-4:R1: 15R; R1210
PPU-V8C1-2:R2, PPU-V8C1-4:R2: 1K; R0805
PPU-V8C1-2:SJ1, PPU-V8C1-4:SJ1: 0R; SJ
PPU-V8C1-2:T1, PPU-V8C1-4:T1: MCAT-SPADE-TERMINAL; SPADE-TERMINAL-FLANGED-NYLON-INSULATED
PPU-V8C1-2:TP1, PPU-V8C1-2:TP2, PPU-V8C1-2:TP3, PPU-V8C1-4:TP1, PPU-V8C1-4:TP2, PPU-V8C1-4:TP3: PCB-MINI-SMD-TESTPOINT/SQ; PCB-MINI-SMD-TESTPOINT
PPU-V8C1-2:U$1, PPU-V8C1-4:U$1: IXDN604/SI; IXYS-SI-8PIN-POWER-SOIC

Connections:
AGND_ADC_GROUND: J4.21, J4.24, PPU-V8C1-2:CT1.3, PPU-V8C1-2:R1.2, PPU-V8C1-4:CT1.3, PPU-V8C1-4:R1.2
CH2_P18H: J4.1, J4.3, J4.5, PPU-V8C1-2:BC1.1, PPU-V8C1-2:BC2.1, PPU-V8C1-2:C1.POS, PPU-V8C1-2:L1.1, PPU-V8C1-2:TP3.1
CH2_P18L: J4.7, J4.9, PPU-V8C1-2:BC3.1, PPU-V8C1-2:BC4.1, PPU-V8C1-2:U$1.6
CH2_SENSE+: J4.22, PPU-V8C1-2:CT1.1, PPU-V8C1-2:R1.1
CH4_P18H: J4.47, J4.49, J4.51, PPU-V8C1-4:BC1.1, PPU-V8C1-4:BC2.1, PPU-V8C1-4:C1.POS, PPU-V8C1-4:L1.1, PPU-V8C1-4:TP3.1
CH4_P18L: J4.43, J4.45, PPU-V8C1-4:BC3.1, PPU-V8C1-4:BC4.1, PPU-V8C1-4:U$1.6
CH4_SENSE+: J4.23, PPU-V8C1-4:CT1.1, PPU-V8C1-4:R1.1
GND: J4.2, J4.4, J4.6, J4.8, J4.10, J4.12, J4.14, J4.42, J4.44, J4.46, J4.48, J4.50, PPU-V8C1-2:BC1.2, PPU-V8C1-2:BC2.2, PPU-V8C1-2:BC3.2, PPU-V8C1-2:BC4.2, PPU-V8C1-2:C1.NEG, PPU-V8C1-2:CT1.PPU-K, PPU-V8C1-2:Q11.E, PPU-V8C1-2:U$1.3, PPU-V8C1-2:U$1.9, PPU-V8C1-4:BC1.2, PPU-V8C1-4:BC2.2, PPU-V8C1-4:BC3.2, PPU-V8C1-4:BC4.2, PPU-V8C1-4:C1.NEG, PPU-V8C1-4:CT1.PPU-K, PPU-V8C1-4:Q11.E, PPU-V8C1-4:U$1.3, PPU-V8C1-4:U$1.9
PPU-V8C1-2:N$2: PPU-V8C1-2:Q11.G, PPU-V8C1-2:R2.2
PPU-V8C1-2:PPU-A: PPU-V8C1-2:L1.2, PPU-V8C1-2:Q11.C, PPU-V8C1-2:T1.T
PPU-V8C1-2:TPIPD_IN: PPU-V8C1-2:SJ1.2, PPU-V8C1-2:TP1.1, PPU-V8C1-2:U$1.2, PPU-V8C1-2:U$1.4
PPU-V8C1-2:TPIPD_OUT: PPU-V8C1-2:R2.1, PPU-V8C1-2:TP2.1, PPU-V8C1-2:U$1.5, PPU-V8C1-2:U$1.7
PPU-V8C1-4:N$2: PPU-V8C1-4:Q11.G, PPU-V8C1-4:R2.2
PPU-V8C1-4:PPU-A: PPU-V8C1-4:L1.2, PPU-V8C1-4:Q11.C, PPU-V8C1-4:T1.T
PPU-V8C1-4:TPIPD_IN: PPU-V8C1-4:SJ1.2, PPU-V8C1-4:TP1.1, PPU-V8C1-4:U$1.2, PPU-V8C1-4:U$1.4
PPU-V8C1-4:TPIPD_OUT: PPU-V8C1-4:R2.1, PPU-V8C1-4:TP2.1, PPU-V8C1-4:U$1.5, PPU-V8C1-4:U$1.7
TP1_OUT: J4.11, J4.13, PPU-V8C1-2:SJ1.1, PPU-V8C1-4:SJ1.1

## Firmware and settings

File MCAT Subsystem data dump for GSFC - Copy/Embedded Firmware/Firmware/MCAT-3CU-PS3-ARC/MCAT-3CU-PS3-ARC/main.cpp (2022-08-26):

/*
 * main.cpp for MCAT-2CU-PS3-OLD
 * for M-CAT 1-ch thruster control unit (Netburner MOD5270B with MOD-DEV-70 eval board)
 * Author: Samudra Haque N3RDX (samudra@gwu.edu)
 */

//////////////////////////////////////////////////// Pin Assignment
/*
 * updated 8/21/2013 SH
 * MOD5270B Pin-Outs with MOD-DEV-70 Board
 * J2-34; SW3 controlling P15H to Ch. 3 PPU V7x
 * J2-36; SW1 controlling P15H to Ch. 1 PPU V7x
 * J2-37; TP  common trigger to all PPU (to be modified later).
 * J2-38; SW2 controlling P15H to Ch. 2 PPU V7x
 */

//////////////////////////////////////////////////// Version History
/*
 * Rev 4G 201308211226 inverted sense of logic for RLY SW 1-3 (Ch. 1 - 3)
 * Rev 4F 201308211003 JD SH with 3 channel and 5 Frequency options
 * Rev 4E 201307251254 testin PPUV8 (FAN3227TMX) timing with 200 uS TP pos width, 200 uS Pre-TP MCH, 200 uS Post-TP MCL
 * Rev 4D 201306111639 testing J2-36 signaling with optocoupler and relay switch
 * Rev 4C 201306091527 tested J2-37 signaling with optocoupler and relay switch
 * Rev 4B 201304011845 general 3V/5V level transl. testing for MCAT-1CU
 * Rev 4A 201304011100 used J2[37] with 74LVX4245 3V/5V level transl. cct.
 * Rev 37C 201303132319 testing GPIO functions w/ disabled DMA timer on MOD-DEV-70
 * Software version continued from GPIOTest application (C6 201208042244)
 * Code includes segments of GPIOTest and test-NB-Semaphore (201208011503)
 *
 * Aug 12 . Julie added pin J2[34] to command PPU number 3
 *
 */

///////////////////////////////////////////////////// Version Block
#define BUILD_MAJOR "4"  // numeric
#define BUILD_MINOR "G" // alpha only
#define BUILD_TIMESTAMP "201308211226"
#define BUILD_APP_TASKMON "M2CU-4G"
#define BUILD_APP_TITLE "Micro-Cathode Arc Thruster 2-Ch Control Unit - Remote Test Program"
#define VERSION_LEN 30
//#define NTP_SERVER_IP "199.241.31.96" //  WARNING Need to select correct time server
#define NTP_SERVER_POOL "0.pool.ntp.org"

////////////////////////////////////////////////////// INCLUDES v
#include "predef.h" //NB template
#include <stdio.h> //NB template
#include <ctype.h> //NB template
#include <startnet.h> //NB template
#include <autoupdate.h> //NB template
#include <dhcpclient.h> //NB template
#include <taskmon.h> //NB template
#include <nbtime.h> /* Include for NTP functions*/
#include <udp.h>
#include <time.h>
#include <string.h>
#include <string>
#include <iosys.h>
#include <utils.h>
/*include for TCP stuff*/
#include <ip.h>
#include <dns.h>
#include <tcp.h>
//#include "clientweb.h"
#include <htmlfiles.h>
#include <ucos.h>
//#include <iostream.h>
//#include <iostream>
#include <pins.h>
#include <sim5270.h> // reqd for ISR
#include <cfinter.h>
#include <math.h>

// Disable SmartTraps when in debug mode
//#ifdef _DEBUG
//#include <NetworkDebug.h>
//#else
//#include <smarttrap.h>
//#endif
#include <smarttrap.h>
using namespace std;

/////////////////////////////////////////////////////////// INCLUDES ^

extern "C" {
    void UserMain(void * pd);
    void displayCLIMenu();
    void displayConfig();
    void doPulses(void *pdata);
    void stopPulses(void *pdata);
    //    void doTP(void *pdata);
    void initDMATIMER1();

    void SetIntc(long func, int vector, int level, int prio); //sets up the 5270 interrupt controller
    void tzsetchar(char * tzenv);
    void ShowLocalIPAddr(int sock, PCSTR url);
    void ShowRemoteIPAddr(int sock, PCSTR url);
    void ShowAppRevision(int sock, PCSTR url);
    void ShowImpulseComponentEvents(int sock, PCSTR url);
    void PrintTimeStruct(struct tm&bt);
    void pollNTPServer();
    void writeTimeStampUTC();
    void htmlDisplayUTCClock(int sock, PCSTR url);
    void setDefaults();
    void disableAll();
}

///////////////////////////////////////////////////////////// GLOBALS

const char * AppName = BUILD_APP_TASKMON;
const char * testString = "Hello World!";
const char
*dow_str[] = { "SUN", "MON", "TUE", "WED", "THU", "FRI", "SAT", "\0" };

char testArrayChars[50] = "Hi, There!";
char gPostBuf[1000]; /// HTML form processing ?

DWORD doPulseStack[USER_TASK_STK_SIZE];
//DWORD doTPStack[USER_TASK_STK_SIZE];
DWORD uint32_counter = 0; //Initalize interrupt counter
DWORD PulseCount = 0; //Initialize whole pulse count
DWORD MaxCount = 1; //Initalize SPC/SPN

IPADDR ntp_srvr_addr; //placeholder for NTP server Ip address (from DNS lookup)

int TS1Count = 0; //DMA TIMER1 Time Step Count
int testVar = { 0 }; // for HTML output
string lastActivityHTML;

bool AssignedDHCP = FALSE; // if DHCP failed.. use static IP addr ?
bool Continuous = FALSE; // variable for SPC=C (HTML UI) condition.

// Semaphore definitions
OS_SEM SemPulse;
OS_SEM SemTP;

// Timing Defaults
//All timing units (IRQCount) are based upon TSR (based upon REFVAL) derived from DMATIMERCALC2.m
//int REFVAL = 67091 for 1.8 mS, 367 for 10 uS;
int TSRD = 367; //Timebase in REFVAL units (TS)
int TSR = TSRD;

/*
 *  * Original source of timing sequence (DMATIMERV2.m) from Taisen Zhuang, 2010-2011
 *


 // TSR timing for each event in sequence
 int MCHCD = 0; //assumed that EMH is turned on at initial, count t=0
 int TPHCD = 182; //Turn on Trigger Pulse at TSR ####
 int TPLCD = 364; //Turn off Trigger Pulse at TSR ####
 int MCLCD = 564; //Turn of Magnetic Coil ####
 int EOCCD = 568; //End of Cycle value - Default 1 Hz
 */

//Following timing block for PPUV7 Hybrid V8 - Samudra 2013 7/30
int MCHCD = 0;
int TPHCD = 30;
int TPLCD = 40;
int MCLCD = 70;
int EOCCD = 99928; // system default F=1 Hz, with the following parameters.

/*Events (inclusive of rise/fall times):
 MCH 0 mS
 TPH 0.3008 mS
 TPL 0.4016 mS
 MCL 0.7024 mS
 EOC 0.710732 mS
 Checking Total time period for 1407 full cycles is: 1 seconds

 [MCF5270 DMA TIMER and Interrupt Count Values]

 Time Step (TSR): 10 uS
 REFVAL: 367
 DIVIDER:1
 PRESCALER:1

 [TS Counter Values (MCHC, TPHC, TPLC, MCLC, EOCC)]
 in ascending order of event time

 0         0
 0.0003   30.0000
 0.0004   40.0000
 0.0007   70.0000
 0.0007   71.0000

 [Table of Frequency vs td (TS Counts)]
 1       99928*/





//Timing components
int MCHC = MCHCD;
int TPHC = TPHCD;
int TPLC = TPLCD;
int MCLC = MCLCD;
int EOCC = EOCCD;

//matching variables for actual time (mS) display through HTML.
double MCHCT = 0;
double TPHCT = 0;
double TPLCT = 0;
double MCLCT = 0;
double EOCCT = 0;
char MCHCTS[5]; //string to hold the value of MCHCTS in X.XX format
char TPHCTS[5];
char TPLCTS[5];
char MCLCTS[5];
char EOCCTS[5];
int DIVIDER = 1;
int PRESCALER = 1;
double INTSYSCLK = 147456000;
double CLOCKFREQ = INTSYSCLK / 2;

// Logic definitions
int HIGH = 1; int NHIGH = 0;
int LOW = 0; int NLOW = 1;

// Pin Selection for SB70LC unused in MOD5270B
//int PINMC = 15; //PTIMER7 //BJT Inverter - could be any pin (SB70LC, JP1-1 to JP1-17)
//int PINTP = 16; //PFECI2C0 //non-inverted be any pin (SB70LC, JP1-1 to JP1-17)
//int PINTP=17; //actually could be any pin (SB70LC, JP1-1 to JP1-17)

int countUP; //interrupt cycle

INTERRUPT(func_isr, 0x2600)
{
    sim.timer[0].ter |= 0x02; //Clear the DTIM0 ref event flag
    // we acknowledge the INTERRUPT, but check first if our PulseCount has exceeded MaxCount
    // meanwhile, the ISR is still running, and can do other functions, the program will not output signals
    // unless desired
    if ((PulseCount < MaxCount) || (Continuous == TRUE)) {
        if (TS1Count == MCHC) {
            //we must activate magnetic coil here MCH
            //Pins[PINMC] = NHIGH; //(inverted) activate magnetic coil
            iprintf("U");
            TS1Count++;
        } else {
            if (TS1Count == TPHC) {
                //Pins[PINTP] = HIGH; //activate trigger pulse
                //Pins[PINTP] = HIGH; //activate trigger pulse
                J2[37].clr(); // inverted due to PPUV7x/V8 hybrid
                ////// test 3V > 5V level transl. - signal TP1 ON
                TS1Count++;
            } else {
                {
                    if (TS1Count == TPLC) {
                        //Pins[PINTP] = LOW; //deactivate trigger pulse
                        //Pins[PINTP] = LOW; //deactivate trigger pulse
                        J2[37].set();
                        //inverted due to PPUV7x/V8 hybrid
                        ////// test 3V > 5V level transl. - signal TP1 OFF
                        TS1Count++;
                    } else {
                        if (TS1Count == MCLC) {
                            //we must deactivate magnetic coil here MCL
                            //Pins[PINMC] = NLOW; //(inverted) deactivate magnetic coil
                            iprintf("D");
                            TS1Count++;
                        } else {

                            if (TS1Count == EOCC) { // end cycle after delay
                                TS1Count = 0; //restart
                                PulseCount++;
                                iprintf(" %d ",PulseCount);
                            } else
                                TS1Count++; //go to next cycle
                        }
                    }
                }
            }
        }
    }
}

void disableAll() {
    iprintf("Z");
    J2[37].clr(); //Set initial state of J2[37] to LOW
    //Pins[PINMC] = NLOW;
    //Pins[PINTP] = LOW;
}

void setDefaults() {
    //reset all params to default Timing components
    iprintf(" ............................ will set defaults now ...\n");
    TSR = TSRD;
    MCHC = MCHCD;
    TPHC = TPHCD;
    TPLC = TPLCD;
    MCLC = MCLCD;
    EOCC = EOCCD;
}

void doPulses(void *pdata) {
    //WORD data = * (WORD *) pdata;
    //iprintf("Data passed to Pulse5(): %d\n",data);
    int pulses;

    while (1) {
        OSSemPend(&SemPulse, 1); //wait forever, then countUP
        pulses = countUP;
        for (int n = 0; n < pulses; n++) {
            iprintf("%d", n);
            //OSTimeDly(TICKS_PER_SECOND); // good to put wait time here.. between pulses.
            iprintf("\n");
            //Toggle the output state of Pin J1-17. Hopefully...
            if (J2[37])
                J2[37].clr(); //if high then toggle low
            else
                J2[37].set(); //if low then toggle high

            //            if (Pins[PINTP])
            //                Pins[PINTP] = LOW; //if high then toggle low
            //            else
            //                Pins[PINTP]; //  toggle high
        }
        //XX OSSemPost(&SemCycleComplete);
    }
}

void displayCLIMenu() {
    iprintf("\r\n--- %s Remote Test Program ---\r\n", BUILD_APP_TASKMON);
    iprintf("--- Micro-Cathode Arc Thruster PhoneSat Experiment/MAPERS [GWU/NASA ARC]\n");
    //pollNTPServer();
    writeTimeStampUTC();
    iprintf("0. Show %s Version\r\n", BUILD_APP_TASKMON);
    iprintf("1. Set F=1 Hz (continuous)\r\n");
    iprintf("2. Set F=2 Hz (continuous)\r\n");
    iprintf("3. Set F=5 Hz (continuous) -- not enabled yet in code \r\n");
    iprintf("4. Set F=7 Hz (continuous) -- not enabled yet in code \r\n");
    iprintf("5. Set F=10 Hz (continuous) -- not enabled yet in code \r\n");
    //iprintf("4. Pulse HIGH/LOW (50%% duty cycle, 1000 times)\r\n");
    iprintf("6. ENABLE MCAT pulse train\r\n");
    iprintf("7. Disable o/p signals\r\n");
    iprintf("8. DISABLE MCAT pulse train\r\n");
    iprintf("9. Restart\r\n");
    iprintf("F. ACTIVATE LED8 & TP1\r\n");
    iprintf("G. DEACTIVATE LED8 & TP1\r\n");
    iprintf("H. ACTIVATE LED1\r\n");
    iprintf("J. DEACTIVATE LED1\r\n");
    iprintf("Z/z. ENABLE/DISABLE uCAT Ch. 1\r\n");
    iprintf("Y/y. ENABLE/DISABLE uCAT Ch. 2\r\n");
    // added by Julie on aug 12
    iprintf("X/x. ENABLE/DISABLE uCAT Ch. 3\r\n");
    iprintf("\n");
}

void displayConfig() {
    iprintf("\r\n%s\n%s (%s.%s) Build (%s)\n", BUILD_APP_TITLE,
            BUILD_APP_TASKMON, BUILD_MAJOR, BUILD_MINOR, BUILD_TIMESTAMP);
    iprintf("Local IP: ");
    ShowIP(EthernetIP);
    iprintf("\n");
}

void initDMATIMER1() {
    TS1Count = 0; //initalize interrupt counter TS1 (DMATIMER1 Time Slice
    sim.timer[0].tmr = 0x001A; //system clock divided by 1
    sim.timer[0].txmr = 0x00;
    sim.timer[0].ter |= 0x02;
    sim.timer[0].trr = TSR * 2; //TSR MATLAB
    sim.timer[0].tcn = 1;
    SetIntc((long) &func_isr, 19, 1, 1);
    sim.timer[0].tmr |= 0x0001; //enable the timer
}

// PrintTimeStruct - Print the time to stdout, which is the debug serial port by default.
void PrintTimeStruct(struct tm &bt) {
    //extern const char * testString;
    iprintf("%d/%d/%d day: %d (%s) %02d:%02d:%02D", bt.tm_mon + 1, bt.tm_mday,
            bt.tm_year + 1900, bt.tm_yday, dow_str[bt.tm_wday], bt.tm_hour,
            bt.tm_min, bt.tm_sec);
}
void writeTimeStampUTC() {
    time_t currentTime;
    struct tm *TIMESTAMP;
    currentTime = time(NULL); //placeholder current sysclock
    TIMESTAMP = gmtime(&currentTime);
    iprintf("Timestamp (UTC): %s\n", asctime(TIMESTAMP));
}
//iprintf(">>>>>>>>>>> %d <<<<<<<<<<<<", TIMESTAMP->tm_year + 1900);

void htmlDisplayUTCClock(int sock, PCSTR url) {
    time_t currentTime;
    struct tm *TIMESTAMP;
    char htmlUTCClock[80];
    // timestamp variables
    int TIMESTAMP_year;
    int TIMESTAMP_mon;
    int TIMESTAMP_day;
    int TIMESTAMP_hour;
    int TIMESTAMP_min;
    int TIMESTAMP_sec;

    currentTime = time(NULL); //placeholder current sysclock
    TIMESTAMP = gmtime(&currentTime);

    TIMESTAMP_year = TIMESTAMP->tm_year + 1900;
    TIMESTAMP_mon = TIMESTAMP->tm_mon + 1;
    TIMESTAMP_day = TIMESTAMP->tm_mday;
    TIMESTAMP_hour = TIMESTAMP->tm_hour;
    TIMESTAMP_min = TIMESTAMP->tm_min;
    TIMESTAMP_sec = TIMESTAMP->tm_sec;
    sprintf(htmlUTCClock, "%d/%d/%d-%d:%d:%d<BR>%s", TIMESTAMP_year,
            TIMESTAMP_mon, TIMESTAMP_day, TIMESTAMP_hour, TIMESTAMP_min,
            TIMESTAMP_sec, BUILD_APP_TASKMON);
    writestring(sock, htmlUTCClock);

}
// IPtoString - Convert IP addr to a string from Pg 74 of NNDK Netburner Programmers Guide
void IPtoString(IPADDR ia, char *s) {
    PBYTE ipb = (PBYTE) &ia;
    siprintf(s, "%d.%d.%d.%d", (int) ipb[0], (int) ipb[1], (int) ipb[2],
             (int) ipb[3]);
}

// Show LocalIPAddr - Simple routine for user comfort when using Web Interface
void ShowLocalIPAddr(int sock, PCSTR url) {
    char buf[80];
    IPtoString(GetSocketLocalAddr(sock), buf);
    writestring(sock, buf);
}

// Display program details on the HTML webpage.
void ShowAppRevision(int sock, PCSTR url) {
    char buf[VERSION_LEN]; //VERSION_LEN = 20 bytes only ! the program will crash if buffer is overrun
    siprintf(buf, "VER: %s(%s)<p> %s", BUILD_MAJOR, BUILD_MINOR,
             BUILD_TIMESTAMP);
    writestring(sock, buf);
}

void ShowRemoteIPAddr(int sock, PCSTR url) {
    char buf[80];
    IPtoString(GetSocketRemoteAddr(sock), buf);
    writestring(sock, buf);
}

// Convert Impulse Component Timing Values in TS to uS.
void ShowImpulseComponentEvents(int sock, PCSTR url) {
    /*
     *
     char buf[VERSION_LEN]; //VERSION_LEN = 20 bytes only ! the program will crash if buffer is overrun
     siprintf(buf, "VER: %s(%s)<p> %s", BUILD_MAJOR, BUILD_MINOR,
     BUILD_TIMESTAMP);
     writestring(sock, buf);
     */

    //refer to MCF5270 DMA TIMER GUIDE
    MCHCT = (MCHC + 1) * (DIVIDER / CLOCKFREQ) * (PRESCALER + 1);
    TPHCT = (TPHC + 1) * (DIVIDER / CLOCKFREQ) * (PRESCALER + 1);
    TPLCT = (TPLC + 1) * (DIVIDER / CLOCKFREQ) * (PRESCALER + 1);
    MCLCT = (MCLC + 1) * (DIVIDER / CLOCKFREQ) * (PRESCALER + 1);
    EOCCT = (EOCC + 1) * (DIVIDER / CLOCKFREQ) * (PRESCALER + 1);
    sprintf(MCHCTS, "%f", MCHCT); //useful for HTML UI
    sprintf(TPHCTS, "%f", TPHCT); //useful for HTML UI
    sprintf(TPLCTS, "%f", TPLCT); //useful for HTML UI
    sprintf(MCLCTS, "%f", MCLCT); //useful for HTML UI
    sprintf(EOCCTS, "%f", EOCCT); //useful for HTML UI
    //printf("DEBUG: Value of MCHC is %f (%g)",MCHCT,MCHCT);
}

void pollNTPServer() {
    /*-------------------------------------------------------------------
     A simple NTP Client example that will get the time from a NTP
     server and display the UTC and PDT time through the debug serial
     port. Use MTTTY to monitor the output.

     For this example to function, your NetBurner device must have
     access to the Internet, with a working configuration for the
     IP address, mask and gateway.
     --------------------------------------------------------------------*/
    DWORD tv = time(NULL);
    struct tm tm_struct;

    struct tm *gmtime_r(const time_t *clock, struct tm *result);
    /*
     Converts a time in seconds since the Epoch (00:00:00 UTC,
     January 1, 1970) into a broken-down time, expressed as
     Coordinated Universal Time (UTC).

     clock  = The time to be converted
     result = Points to the structure where the converted time is to be stored

     On success, gmtime_r() return result. On error, it returns NULL
     */

    gmtime_r((const time_t *) &tv, &tm_struct);
    iprintf("UTC time = ");
    PrintTimeStruct(tm_struct);

    tzsetchar("EST5EDT4,M3.2.0/01:00:00,M11.1.0/02:00:00");

    localtime_r((const time_t *) &tv, &tm_struct);
    iprintf("\r\n%s time = ", _tzname[0]);
    PrintTimeStruct(tm_struct);
    iprintf("\r\n\r\n");

    testVar++; //increment counter to display on HTML webpage.
}

void UserMain(void * pd) {
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

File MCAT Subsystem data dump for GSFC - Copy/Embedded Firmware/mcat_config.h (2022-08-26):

/*
 * mcat_config.h - C++ header file for MCAT-4CU controller
 *
 * Copyright 2014-2015 The George Washington University. ALL RIGHTS RESERVED. Patents Pending
 * Author: Samudra Haque (SH), G19124781, N3RDX, samudra@gwu.edu, samudra.haque@gmail.com
 * 9/25/2014
 */

#ifndef MCAT_CONFIG_H_
#define MCAT_CONFIG_H_



#define GROUNDTESTING //define GROUNDTESTING for extra messages, or comment out this line if not needed

//general variables
char stringVersion[2];


//define DMA TIMER section relevant values
DWORD doPulseStack[USER_TASK_STK_SIZE];
DWORD uint32_counter = 0;
DWORD PulseCount = 0;
DWORD MaxCount = 1;
DWORD endCountCh1 = 0;
DWORD endCountCh2 = 0;
DWORD endCountCh3 = 0;
DWORD endCountCh4 = 0;
int TS1Count = 0;
bool Continuous = FALSE;
OS_SEM SemPulse;
OS_SEM SempTP;


//uCOS task section relevant values
OS_SEM P18H1Sem, P18H2Sem, P18H3Sem, P18H4Sem;
int Ch1Prio=62;//recommend user priority 46 to 62, 46 >> 62 priority
int Ch2Prio=61;
int Ch3Prio=60;
int Ch4Prio=59;

//logic definitions
int HIGH=1; int NHIGH = 0;
int LOW=0; int NLOW = 1;
int ON=1; int OFF = 0;
int ACTIVE=1; int INACTIVE=0;

int countUP; //interrupt cycle

#define MCAT_PPU_CHANNELS 4 // number of PPU channels
#define TEST_PULSE_COUNT 5 //min number of counts per test run

#ifdef TESTCU
#include <pins.h>
#include <bsp.h>
//GPIO PIN definition TESTCU
#define SW_RUNPMA Pins[23]
#define SW_TP1 Pins[12]
#define SW_P18L12 Pins[16]
#define SW_P18H12 Pins[25]
#define SW_P18L34 Pins[49]
#define SW_P18H34 Pins[50]
#else
#ifdef FLTCU
#include <pins.h>
//GPIO PIN definition FLTCU
#define SW_RUNPMA Pins[23]
#define SW_TP1 Pins[31]
#define SW_P18H4 Pins[32]
#define SW_P18H3 Pins[33]
#define SW_P18H2 Pins[34]
#define SW_P18H1 Pins[35]
#define SW_P18L4 Pins[36]
#define SW_P18L3 Pins[37]
#define SW_P18L2 Pins[38]
#define SW_P18L1 Pins[39]

#define SW_P18L12 Pins[99]
#define SW_P18H12 Pins[99]
#define SW_P18L34 Pins[99]
#define SW_P18H34 Pins[99]

#endif //FLTCU
#endif //TESTCU

/*
* TESTBUS (MOD54415), TESTCU (NANO54414)/FLTCU (NANO54414) I2C address
*/
#define CU_I2C_SLAVE_ADDR 0x26 // hardcoded I2C slave address.
#define TESTBUS_I2C_SLAVE_ADDR 0x24 //hardcoded I2C slave address

/*
* TESTCU/FLTCUsoftware build information
*/
#define CU_SUBSYSTEM "MCAT-4CU-B Subsystem" //root name of proj.
#define CU_PROJECT "Micro-Cathode Arc Thruster Subsystem for USNA BRICSAT-p Cubesat" //add an extra leading space here for formatting
#define CU_BUILD_MAJOR "6"  // numeric single digit
#define CU_BUILD_MINOR "C" // alpha only single digit
#define CU_AUTHOR " samudra@gwu.edu N3RDX"
/*
 * special config for USNA Bricsat mission
 */
#define BRICSAT
#define HIDDENMENU

#ifdef BRICSAT
DWORD limitPulseCount = 50; //stop at pulses

#else
DWORD limitPulseCount = 0; //effectively we pulse continuously
#endif //BRICSAT

//history
//A - initial version
//B - conditional defines for TESTCU and FLTCU configuration 10/22/2014 SH MPNL
#define CU_VERSION_LEN 10 //numeric

/* history of TESTCU/FLTCU
 * Version 5A was the First Light configuration of MCAT-4CU with 2 x MCAT-2C boards in correct configuration. 10/6/2014 @2000
 * Version 6A test version for general software commands checkout and adjustment of trigger pulse timing.
 */

/*
* TESTBUS software build information
*/
#define TB_BUILD_MAJOR "1"  // numeric
#define TB_BUILD_MINOR "A" // alpha only
#define TB_VERSION_LEN 10 //numeric

/*
* General Build Information
*/
#define BUILD_TIMESTAMP "201409251844"
#define BUILD_APP_TASKMON "M2CU-4G"
#define BUILD_APP_TITLE "Micro-Cathode Arc Thruster 2-Ch Control Unit - Remote Test Program"
#define BUILD_DATE __DATE__
#define BUILD_TIME __TIME__


#endif /* MCAT_CONFIG_H_ */

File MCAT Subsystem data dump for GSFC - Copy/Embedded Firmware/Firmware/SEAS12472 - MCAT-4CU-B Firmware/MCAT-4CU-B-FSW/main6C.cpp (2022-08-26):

/*****************************************************************************
 *
 * TESTCU/FLTCU shared main.cpp for GWU MpNL's Micro-Cathode Arc Thruster (MCAT) Subsystem
 *
 * Copyright 2014-2015 The George Washington University. ALL RIGHTS RESERVED. Patents Pending
 * Author: Samudra Haque (SH), G19124781, N3RDX, samudra@gwu.edu, samudra.haque@gmail.com
 * 9/25/2014
 *
 * Incorporating: adaptations from Netburner Inc. "MOD5270 I2CSerial" sample program.
 * Incorporating: modifications by SH to accomodate multichanneli2c.h instead of i2cmulti.h
 *
 * The FSW I2C operates in SLAVE mode.
 * This NBECLIPSE build configuration is in two modes:
 *    TESTCU - for NANO54415 in NANO Carrier Board Rev 1.3 (Netburner)
 *    FLTCU - for NANO54415 in MCAT-4CU-B-V2K1 contro18Ler Board (GWU)
 *
 * When choosing TESTCU - you will have support for Ethernet, GPIO etc. available on the NANO carrier board
 *
 */



/*
 #ifdef NANO54415
 #error DOUBLE WOW NANO54415 is defined !!!!
 #else
 #ifdef MCF5441X
 #error WOW MCF5441X constant is defined !!!!
 #endif
 #endif
 */



#include "predef.h"
#include <stdio.h>
#include <ctype.h>
#include <startnet.h>
#include <autoupdate.h>
#include <dhcpclient.h>
#include <taskmon.h>
#include <smarttrap.h>
#include <string.h>
#include <math.h>


/*
 * Includes and defines for MCAT-4CU-B-FSW codebase
 */
#include <assert.h>
#include <multichanneli2c.h> //modified by SH 9/21/14 only for NANO54414
#include <sim5441x.h>
//#include <ucos.h>
#include <cfinter.h>
#include <iostream>
#include <iomanip>
#include <string>
#include "mcat_config.h" //all variables
#include "mcat_cmd_packet.h" //MCAT Command Packet Specs
#include "mcat_timing.h" //MCAT Trigger Pulse Specs
#include "periph_clocks.h" //from netburner for disabling peripherals

using namespace std;

/*
 * GLOBAL VARIABLES
 */
DWORD startPulseCount, endPulseCount;
BOOL toggleHFlag;
char idQ[80]; //quick query ID string
char idCU[160]; //identifier string for the control unit
char verCU[2]; //version number
string cmdVersion=""; //string of command packet version
string cmdMode=""; //string of command mode to be set
string cmdModeCurrent=""; //string of command mode the system is currently in.
string s_freqTP1=""; //string of Trigger Pulse 1 Frequency
string s_freqTP2=""; //string of Trigger Pulse 2 Frequency (future use only)
string s_freqTP3=""; //string of Trigger Pulse 3 Frequency (future use only)
string s_freqTP4=""; //string of Trigger Pulse 4 Frequency (future use only)
string s_countCh1="";//string of Channel 1 pulse count to be executed
string s_countCh2="";//string of Channel 2 pulse count to be executed
string s_countCh3="";//string of Channel 3 pulse count to be executed
string s_countCh4="";//string of Channel 4 pulse count to be executed
//numeric values for the Frequency and Pulse Counts
long freqTP1 = 10;
long freqTP2 = 10;
long freqTP3 = 10;
long freqTP4 = 10;
long countCh1 = 0;
long countCh2 = 0;
long countCh3 = 0;
long countCh4 = 0;
string s_cmdP18H1="";//string of fire command for PPU1
string s_cmdP18H2="";//string of fire command for PPU2
string s_cmdP18H3="";//string of fire command for PPU3
string s_cmdP18H4="";//string of fire command for PPU4
bool cmdP18H1, cmdP18H2, cmdP18H3, cmdP18H4;//boolean flags for the PPUx firing commands, one per ch.

/*
 * Function defines
 */

void parseCMDPacket (char CMDPacket[I2C_MAX_BUF_SIZE]);
void parseBlockG (string BlockG);
void parseBlockCU (string BlockCU);
void parseBlockIPD (string BlockIPD);
void parseBlockPPU (string BlockPPU);

BYTE Ascii2Byte(char *buf);
void menu(void);

// Instruct the C++ compiler not to mangle the function name
extern "C" {
void UserMain(void * pd);
//void displayCLIMenu();
void displayConfig();
//void doPulses(void *pdata);
void stopPulses(void *pdata);
//    void doTP(void *pdata);
void initDMATIMER1();

void SetIntc(long func, int vector, int level, int prio); //sets up the 5270/54415 interrupt contro18Ler
// void tzsetchar(char * tzenv);
//void ShowLocalIPAddr(int sock, PCSTR url);
//void ShowRemoteIPAddr(int sock, PCSTR url);
// void ShowAppRevision(int sock, PCSTR url);
//void ShowImpulseComponentEvents(int sock, PCSTR url);
// void PrintTimeStruct(struct tm&bt);
//void pollNTPServer();
//void writeTimeStampUTC();
// void htmlDisplayUTCClock(int sock, PCSTR url);
void setDefaults();
void disableAll();


}

// Name for development tools to identify this application
#ifdef TESTCU
const char *AppName = "TESTCU";
#warning TESTCU build in progress ----------------------------------------------
#else
#ifdef FLTCU
const char *AppName = "FLTCU";
#warning FLTCU build in progress ----------------------------------------------
#else
#error Choose FLTCU or TESTCU
#endif
#endif

//globals below
BYTE buffer[I2C_MAX_BUF_SIZE];
char I2CInputBuffer[I2C_MAX_BUF_SIZE]; // User-created I2C input buffer
char *inbuf = I2CInputBuffer; // Pointer to user I2C buffer
BYTE address = CU_I2C_SLAVE_ADDR; //assigned I2C Slave Address for this Control Unit
BYTE I2CStat;
string menuVersion;
//globals above



void debugPrint(string debugMsg){
#ifdef GROUNDTESTING
	cout << endl <<  __FILE__ << " / " << __LINE__ << " / " << __func__ << "[" << debugMsg << "]" << endl;
#endif
}
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

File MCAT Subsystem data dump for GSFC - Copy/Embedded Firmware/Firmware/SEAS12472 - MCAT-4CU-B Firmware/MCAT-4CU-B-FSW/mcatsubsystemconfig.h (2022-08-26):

/*
 * mcatsubsystemconfig.h
 *
 * Copyright 2014-2015 The George Washington University. ALL RIGHTS RESERVED. Patents Pending
 * Author: Samudra Haque (SH), G19124781, N3RDX, samudra@gwu.edu, samudra.haque@gmail.com
 * 9/25/2014
 */

#ifndef MCATSUBSYSTEMCONFIG_H_
#define MCATSUBSYSTEMCONFIG_H_

#define CU_I2C_SLAVE_ADDR 0x26 // hardcoded I2C slave address.
#define TESTBUS_I2C_SLAVE_ADDR 0x24 //hardcoded test I2C master address
#define MCAT_I2C_CMD_PACKET_LEN 34

char MCAT_CMD[4]; //4 chars for each command IDLE, STBY, ENTP, ENTC, DITC, DITP
/*
 * IDLE - Go to Idle Mode .. CU command block
 * STBY - Go to Standby Mode .. PM command block
 * ENTP - Enable Trigger Pulse(s) .. Trigger Pulses (TP), IGBT Pre-Driver (IPD) and P18L command block
 * ENTC - Enable Thruster Channel(s) .. P18H command block
 * DITC - Disable Thruster Channel(s) .. P18H command block
 * DITP - Disable Trigger Pulses (TP, IPD, P18L command block)
 *
 */
#define MCAT_CMD_GO_IDLE_MODE 'IDLE' //limited to 4 characters
#define MCAT_CMD_GO_STANDBY_MODE "STBY"
#define MCAT_CMD_ENABLE_TRIGGER_PULSES "ENTP"
#define MCAT_CMD_ENABLE_THRUSTER_CHANNELS "ENTC"
#define MCAT_CMD_DISABLE_THRUSTER_CHANNELS "DITC"
#define MCAT_CMD_DISABLE_TRIGGER_PULSES "DITP"

char MCAT_CMD_QUERY[4]; //4 chars for each type of status inquiry
/*
 * TLM1 - Telemetry Enquiry - single response requested
 * TLMC - Telemetry Enquiry - continuous response requested
 * TLMS - Stop Telemetry feed
 */
#define MCAT_CMD_QUERY_TLM_SINGLE "TLM1"
#define MCAT_CMD_QUERY_TLM_CONTINUOUS "TLMC"
#define MCAT_CMD_QUERY_TLM_STOP "TLMS"


#define BUILD_MAJOR "5"  // numeric
#define BUILD_MINOR "A" // alpha only
#define VERSION_LEN 10 //numeric

#define BUILD_TIMESTAMP "201409251844"
#define BUILD_APP_TASKMON "M2CU-4G"
#define BUILD_APP_TITLE "Micro-Cathode Arc Thruster 2-Ch Control Unit - Remote Test Program"


#include <iostream>
#include <iomanip>
#include <string>
using namespace std;

//MCAT CMD parameter defines V1
#define MCAT_CMD_VERSION_LEN 2 //bytes
#define MCAT_CMD_MODE_LEN 3 //bytes


//Block - General
#define DEF_CMD_VERSION "V1"
//Block - CU - Control Unit section
#define LEN_CMD_CU //whole section
#define LEN_CMD_CU_BITE 1 //bytes, built in test equipment
#define LEN_CMD_CU_TIME 4 //bytes time_t
//predefined values for the sub-commands
#define MODE_CHANGE_TO_IDLE "M11"
#define MODE_CHANGE_TO_STANDBY "M21"
#define DEF_CMD_CU_TIME "0000"

//Block - PM - Power Management section
#define LEN_CMD_PM 2 //whole section
#define LEN_CMD_PM_BITE //bytes, built in test equipment

//Block - IPD - IGBT Pre-Driver section
#define LEN_CMD_IPD 2 //whole section
#define LEN_CMD_IPD_BITE //bytes, built in test equipment

//Block - PPU - Plasma Power Unit section
#define LEN_CMD_PPU 2 //whole section
#define LEN_CMD_PPU_BITE //bytes, built in test equipment

//Block - MNPS - MxN Power Switch section
#define LEN_CMD_MNPS 2 //whole section
#define LEN_CMD_MNPS_BITE //bytes, built in test equipment

//Block - SENS - Sensors Section
#define LEN_CMD_SENSORS 2 //whole section
#define LEN_CMD_SENSORS_BITE //bytes, built in test equipment

//delete me
#define MCAT_CMD_QUERY_TLM_STOP "TLMS"


#endif /* MCATSUBSYSTEMCONFIG_H_ */

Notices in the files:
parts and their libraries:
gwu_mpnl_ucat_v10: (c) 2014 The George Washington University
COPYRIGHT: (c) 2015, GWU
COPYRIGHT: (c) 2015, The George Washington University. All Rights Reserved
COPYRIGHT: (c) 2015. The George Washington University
